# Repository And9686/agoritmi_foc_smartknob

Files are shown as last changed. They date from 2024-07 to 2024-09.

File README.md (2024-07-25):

# Algoritmi SmartKnob DevKit
## Motivation
This repository intends to achieve a development kit for a SmartKnob like the one from scottbez and allow it to be compatible with any microcontroller with dedicated firmware adaptable to any board. This DevKit design is inspired by NanoFoc DevKit by KatBinaris.

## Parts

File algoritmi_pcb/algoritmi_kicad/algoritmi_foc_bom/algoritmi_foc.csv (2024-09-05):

Reference | Value | Datasheet | Footprint | Qty | DNP | Manufacturer_Part_Number | Mouser Part Number | LCSC Electronics Part Number
C1 | 100nF 50V | http://www.samsungsem.com/kr/support/product-search/mlcc/CL10B104KB8NNWC.jsp | CAPC1608X90N | 1 |  | CL10B104KB8NNWC | 187-CL10B104KB8NNWC
C2 | 100nF 50V | http://www.samsungsem.com/kr/support/product-search/mlcc/CL10B104KB8NNWC.jsp | CAPC1608X90N | 1 |  | CL10B104KB8NNWC | 187-CL10B104KB8NNWC
C3 | 100nF 50V | http://www.samsungsem.com/kr/support/product-search/mlcc/CL10B104KB8NNWC.jsp | CAPC1608X90N | 1 |  | CL10B104KB8NNWC | 187-CL10B104KB8NNWC
C4 | 100nF 50V | http://www.samsungsem.com/kr/support/product-search/mlcc/CL10B104KB8NNWC.jsp | CAPC1608X90N | 1 |  | CL10B104KB8NNWC | 187-CL10B104KB8NNWC
C5 | 10uF 25V | https://datasheet.datasheetarchive.com/originals/distributors/Datasheets_SAMA/6a45835c9b7400e9b49c55c38a8ff4a2.pdf | CAPC2012X145N | 1 |  | CL21A106KAYNNNE | 187-CL21A106KAYNNNE
C7 | 4.7uF 25V | https://psearch.en.murata.com/capacitor/product/GCM21BC71E475KE36%23.html | CAPC2012X140N | 1 |  | GCM21BC71E475KE36K | 81-GCM21BC71E475KE6K
C8 | 4.7uF 25V | https://psearch.en.murata.com/capacitor/product/GCM21BC71E475KE36%23.html | CAPC2012X140N | 1 |  | GCM21BC71E475KE36K | 81-GCM21BC71E475KE6K
C9 | 10uF 25V | https://datasheet.datasheetarchive.com/originals/distributors/Datasheets_SAMA/6a45835c9b7400e9b49c55c38a8ff4a2.pdf | CAPC2012X145N | 1 |  | CL21A106KAYNNNE | 187-CL21A106KAYNNNE
C10 | 100nF 50V | http://www.samsungsem.com/kr/support/product-search/mlcc/CL10B104KB8NNWC.jsp | CAPC1608X90N | 1 |  | CL10B104KB8NNWC | 187-CL10B104KB8NNWC
D1 | STDBY | https://datasheet.datasheetarchive.com/originals/distributors/Datasheets_SAMA/f235664866caa647598714bb71411137.pdf | LEDM1620X150N | 1 |  | SML-D12M8WT86 | 755-SML-D12M8WT86
D2 | ERROR | https://datasheet.datasheetarchive.com/originals/distributors/Datasheets_SAMA/f235664866caa647598714bb71411137.pdf | LEDM1620X150N | 1 |  | SML-D12M8WT86 | 755-SML-D12M8WT86
IC2 | AP2114HA-3.3TRG1 | https://www.diodes.com//assets/Datasheets/AP2114.pdf | SOT230P700X180-4N | 1 |  | AP2114HA-3.3TRG1 | 621-AP2114HA-3.3TRG1
J1 | ~ |  | solder_pads:solder_pads_2mm_8 | 1 | DNP |  | 1
J2 | 53261-0371 |  | 532610371 | 1 |  | 53261-0371 | 538-53261-0371
J3 | SMM-115-02-S-D-LC-K-TR | https://suddendocs.samtec.com/prints/smm-1xx-xx-xx-d-xx-xx-x-xx-mkt.pdf | SMM11502SDLCKTR | 1 |  | SMM-115-02-S-D-LC-K-TR | 200-SMM11502SDLCKTR
MSW1 | ~ |  | solder_pads:solder_pads_4mm_3 | 1 |  |  | 906-XCF3Z1
MSW2 | ~ |  | solder_pads:solder_pads_4mm_3 | 1 |  |  | 906-XCF3Z1
MSW3 | ~ |  | solder_pads:solder_pads_4mm_3 | 1 |  |  | 906-XCF3Z1
MSW4 | ~ |  | solder_pads:solder_pads_4mm_3 | 1 |  |  | 906-XCF3Z1
R1 | 300R | https://industrial.panasonic.com/cdbs/www-data/pdf/RDP0000/AOA0000C337.pdf | ERJUP3 | 1 |  | ERJ-UP3F3000V | 667-ERJ-UP3F3000V
R2 | 300R | https://industrial.panasonic.com/cdbs/www-data/pdf/RDP0000/AOA0000C337.pdf | ERJUP3 | 1 |  | ERJ-UP3F3000V | 667-ERJ-UP3F3000V
R3 | 150m | https://www.koaspeer.com/pdfs/UR73V.pdf | RESC3216X70N | 1 |  | UR73VH2BTTDR150F | 660-UR73VH2BTTDR150F
R4 | 150m | https://www.koaspeer.com/pdfs/UR73V.pdf | RESC3216X70N | 1 |  | UR73VH2BTTDR150F | 660-UR73VH2BTTDR150F
R5 | 100K | https://www.mouser.co.uk/datasheet/2/54/Bourns_CMP_Datasheet_05.28.20-1854233.pdf | RESC1608X55N | 1 |  | CMP0603-FX-1003ELF | 652-CMP0603-FX-1003L
R6 | 100K | https://www.mouser.co.uk/datasheet/2/54/Bourns_CMP_Datasheet_05.28.20-1854233.pdf | RESC1608X55N | 1 |  | CMP0603-FX-1003ELF | 652-CMP0603-FX-1003L
R7 | 100K | https://www.mouser.co.uk/datasheet/2/54/Bourns_CMP_Datasheet_05.28.20-1854233.pdf | RESC1608X55N | 1 |  | CMP0603-FX-1003ELF | 652-CMP0603-FX-1003L
R8 | 100K | https://www.mouser.co.uk/datasheet/2/54/Bourns_CMP_Datasheet_05.28.20-1854233.pdf | RESC1608X55N | 1 |  | CMP0603-FX-1003ELF | 652-CMP0603-FX-1003L
R9 | 100K | https://www.mouser.co.uk/datasheet/2/54/Bourns_CMP_Datasheet_05.28.20-1854233.pdf | RESC1608X55N | 1 |  | CMP0603-FX-1003ELF | 652-CMP0603-FX-1003L
R10 | 100K | https://www.mouser.co.uk/datasheet/2/54/Bourns_CMP_Datasheet_05.28.20-1854233.pdf | RESC1608X55N | 1 |  | CMP0603-FX-1003ELF | 652-CMP0603-FX-1003L
R11 | 300R | https://industrial.panasonic.com/cdbs/www-data/pdf/RDP0000/AOA0000C337.pdf | ERJUP3 | 1 |  | ERJ-UP3F3000V | 667-ERJ-UP3F3000V
R12 | 300R | https://industrial.panasonic.com/cdbs/www-data/pdf/RDP0000/AOA0000C337.pdf | ERJUP3 | 1 |  | ERJ-UP3F3000V | 667-ERJ-UP3F3000V
R13 | 300R | https://industrial.panasonic.com/cdbs/www-data/pdf/RDP0000/AOA0000C337.pdf | ERJUP3 | 1 |  | ERJ-UP3F3000V | 667-ERJ-UP3F3000V
R14 | 300R | https://industrial.panasonic.com/cdbs/www-data/pdf/RDP0000/AOA0000C337.pdf | ERJUP3 | 1 |  | ERJ-UP3F3000V | 667-ERJ-UP3F3000V
U1 | TMC6300-LA-T | TMC6300-LA-T | SamacSys_Parts:QFN40P300X300X90-21N | 1 |  | TMC6300-LA-T | 700-TMC6300-LA-T
U2 | MT6701CT-STD | https://www.lcsc.com/datasheet/lcsc_datasheet_2109011830_Magn-Tek-MT6701CT-STD_C2856764.pdf | Package_SO:SOIC-8_3.9x4.9mm_P1.27mm | 1 |  | MT6701CT-STD |  | C2856764

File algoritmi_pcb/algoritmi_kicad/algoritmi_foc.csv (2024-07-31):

Source: | C:\Users\aluno\Documents\GitHub\agoritmi_foc_smartknob\algoritmi_pcb\algoritmi_kicad\algoritmi_foc.kicad_sch
Date: | 7/31/2024 11:25:34 AM
Tool: | Eeschema 7.0.10
Generator: | C:\Program Files\KiCad\7.0\bin\scripting\plugins/bom_csv_grouped_by_value.py
Component Count: | 35
Collated Components:
Item | Qty | Reference(s) | Value | LibPart | Footprint | Datasheet | DNP | Height | Link | Manufacturer_Name | Manufacturer_Part_Number | Mouser | Mouser Part Number | Mouser Price/Stock
1 | 4 | C1, C2, C3, C4 | 100nF 50V | :CL10B104KB8NNWC_1 | CAPC1608X90N | http://www.samsungsem.com/kr/support/product-search/mlcc/CL10B104KB8NNWC.jsp |  | 0.9 |  | SAMSUNG | CL10B104KB8NNWC |  | 187-CL10B104KB8NNWC | https://www.mouser.co.uk/ProductDetail/Samsung-Electro-Mechanics/CL10B104KB8NNWC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
2 | 1 | C5 | 10uF 25V | :CL21A106KAYNNNE_1 | CAPC2012X145N | https://datasheet.datasheetarchive.com/originals/distributors/Datasheets_SAMA/6a45835c9b7400e9b49c55c38a8ff4a2.pdf |  | 1.45 |  | SAMSUNG | CL21A106KAYNNNE |  | 187-CL21A106KAYNNNE | https://www.mouser.co.uk/ProductDetail/Samsung-Electro-Mechanics/CL21A106KAYNNNE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
3 | 1 | C6 | 1uF | SamacSys_Parts:CL10A105KA8NNNC | CAPC1608X90N |  |  | 0.9 |  | SAMSUNG | CL10A105KA8NNNC |  | 187-CL10A105KA8NNNC | https://www.mouser.co.uk/ProductDetail/Samsung-Electro-Mechanics/CL10A105KA8NNNC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
4 | 2 | C7, C8 | 4.7uF 25V | :GCM21BC71E475KE36K_1 | CAPC2012X140N | https://psearch.en.murata.com/capacitor/product/GCM21BC71E475KE36%23.html |  | 1.4 |  | Murata Electronics | GCM21BC71E475KE36K |  | 81-GCM21BC71E475KE6K | https://www.mouser.co.uk/ProductDetail/Murata-Electronics/GCM21BC71E475KE36K?qs=dNBNMwHp2UBfaO4Bu7xrag%3D%3D
5 | 1 | C9 | 10uF 25V | SamacSys_Parts:CL21A106KAYNNNE | CAPC2012X145N | https://datasheet.datasheetarchive.com/originals/distributors/Datasheets_SAMA/6a45835c9b7400e9b49c55c38a8ff4a2.pdf |  | 1.45 |  | SAMSUNG | CL21A106KAYNNNE |  | 187-CL21A106KAYNNNE | https://www.mouser.co.uk/ProductDetail/Samsung-Electro-Mechanics/CL21A106KAYNNNE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
6 | 1 | D1 | STDBY | :SML-D12M8WT86_2 | LEDM1620X150N | https://datasheet.datasheetarchive.com/originals/distributors/Datasheets_SAMA/f235664866caa647598714bb71411137.pdf |  | 1.5 |  | ROHM Semiconductor | SML-D12M8WT86 |  | 755-SML-D12M8WT86 | https://www.mouser.co.uk/ProductDetail/ROHM-Semiconductor/SML-D12M8WT86?qs=4kLU8WoGk0vGWtDreJ93zQ%3D%3D
7 | 1 | D2 | ERROR | :SML-D12M8WT86_1 | LEDM1620X150N | https://datasheet.datasheetarchive.com/originals/distributors/Datasheets_SAMA/f235664866caa647598714bb71411137.pdf |  | 1.5 |  | ROHM Semiconductor | SML-D12M8WT86 |  | 755-SML-D12M8WT86 | https://www.mouser.co.uk/ProductDetail/ROHM-Semiconductor/SML-D12M8WT86?qs=4kLU8WoGk0vGWtDreJ93zQ%3D%3D
8 | 1 | IC1 | MA710GQ-Z | SamacSys_Parts:MA710GQ-Z | QFN50P300X300X100-17N-D |  |  | 1 |  | Monolithic Power Systems (MPS) | MA710GQ-Z |  | 946-MA710GQ-Z | https://www.mouser.co.uk/ProductDetail/Monolithic-Power-Systems-MPS/MA710GQ-Z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
9 | 1 | IC2 | AP2114HA-3.3TRG1 | SamacSys_Parts:AP2114HA-3.3TRG1 | SOT230P700X180-4N | https://www.diodes.com//assets/Datasheets/AP2114.pdf |  | 1.8 |  | Diodes Incorporated | AP2114HA-3.3TRG1 |  | 621-AP2114HA-3.3TRG1 | https://www.mouser.co.uk/ProductDetail/Diodes-Incorporated/AP2114HA-3.3TRG1?qs=M%2FOdCRO8QQ3KWhA9Gt6VoQ%3D%3D
10 | 1 | J1 | ~ | solder_pad:solder_pad_2mm_8 | solder_pads:solder_pads_2mm_8
11 | 1 | J2 | 53261-0371 | SamacSys_Parts:53261-0371 | 532610371 |  |  | 3.6 |  | Molex | 53261-0371 |  | 538-53261-0371 | https://www.mouser.co.uk/ProductDetail/Molex/53261-0371?qs=%252B72YyncTwW%252BTQBxAO1kJjA%3D%3D
12 | 1 | J3 | SMM-115-02-S-D-LC-K-TR | SamacSys_Parts:SMM-115-02-S-D-LC-K-TR | SMM11502SDLCKTR | https://suddendocs.samtec.com/prints/smm-1xx-xx-xx-d-xx-xx-x-xx-mkt.pdf |  | 3.81 |  | SAMTEC | SMM-115-02-S-D-LC-K-TR |  | 200-SMM11502SDLCKTR | https://www.mouser.co.uk/ProductDetail/Samtec/SMM-115-02-S-D-LC-K-TR?qs=Cqqh%252BS766wmCL5XLNTE7Jg%3D%3D
13 | 4 | MSW1, MSW2, MSW3, MSW4 | ~ | solder_pad:solder_pad_4mm_3 | solder_pads:solder_pads_4mm_3 |  |  |  | https://pt.mouser.com/ProductDetail/Saia-Burgess/XCF3Z1?qs=lDMevKbHVysAJU%252Bj62uRPA%3D%3D |  |  | 906-XCF3Z1
14 | 2 | R1, R2 | 300R | :ERJ-UP3F3000V_1 | ERJUP3 | https://industrial.panasonic.com/cdbs/www-data/pdf/RDP0000/AOA0000C337.pdf |  | 0.55 |  | Panasonic | ERJ-UP3F3000V |  | 667-ERJ-UP3F3000V | https://www.mouser.co.uk/ProductDetail/Panasonic/ERJ-UP3F3000V?qs=GedFDFLaBXGMAT9BybhSQA%3D%3D
15 | 2 | R3, R4 | 150m | :UR73VH2BTTDR150F_1 | RESC3216X70N | https://www.koaspeer.com/pdfs/UR73V.pdf |  | 0.7 |  | KOA Speer | UR73VH2BTTDR150F
16 | 6 | R5, R6, R7, R8, R9, R10 | 100K | :CMP0603-FX-1003ELF_1 | RESC1608X55N | https://www.mouser.co.uk/datasheet/2/54/Bourns_CMP_Datasheet_05.28.20-1854233.pdf |  | 0.55 |  | Bourns | CMP0603-FX-1003ELF |  | 652-CMP0603-FX-1003L | https://www.mouser.co.uk/ProductDetail/Bourns/CMP0603-FX-1003ELF?qs=TiOZkKH1s2SZ50zoNdROqA%3D%3D
17 | 4 | R11, R12, R13, R14 | 300R | SamacSys_Parts:ERJ-UP3F3000V | ERJUP3 | https://industrial.panasonic.com/cdbs/www-data/pdf/RDP0000/AOA0000C337.pdf |  | 0.55 |  | Panasonic | ERJ-UP3F3000V |  | 667-ERJ-UP3F3000V | https://www.mouser.co.uk/ProductDetail/Panasonic/ERJ-UP3F3000V?qs=GedFDFLaBXGMAT9BybhSQA%3D%3D
18 | 1 | U1 | TMC6300-LA-T | TMC6300:TMC6300-LA-T | SamacSys_Parts:QFN40P300X300X90-21N | TMC6300-LA-T

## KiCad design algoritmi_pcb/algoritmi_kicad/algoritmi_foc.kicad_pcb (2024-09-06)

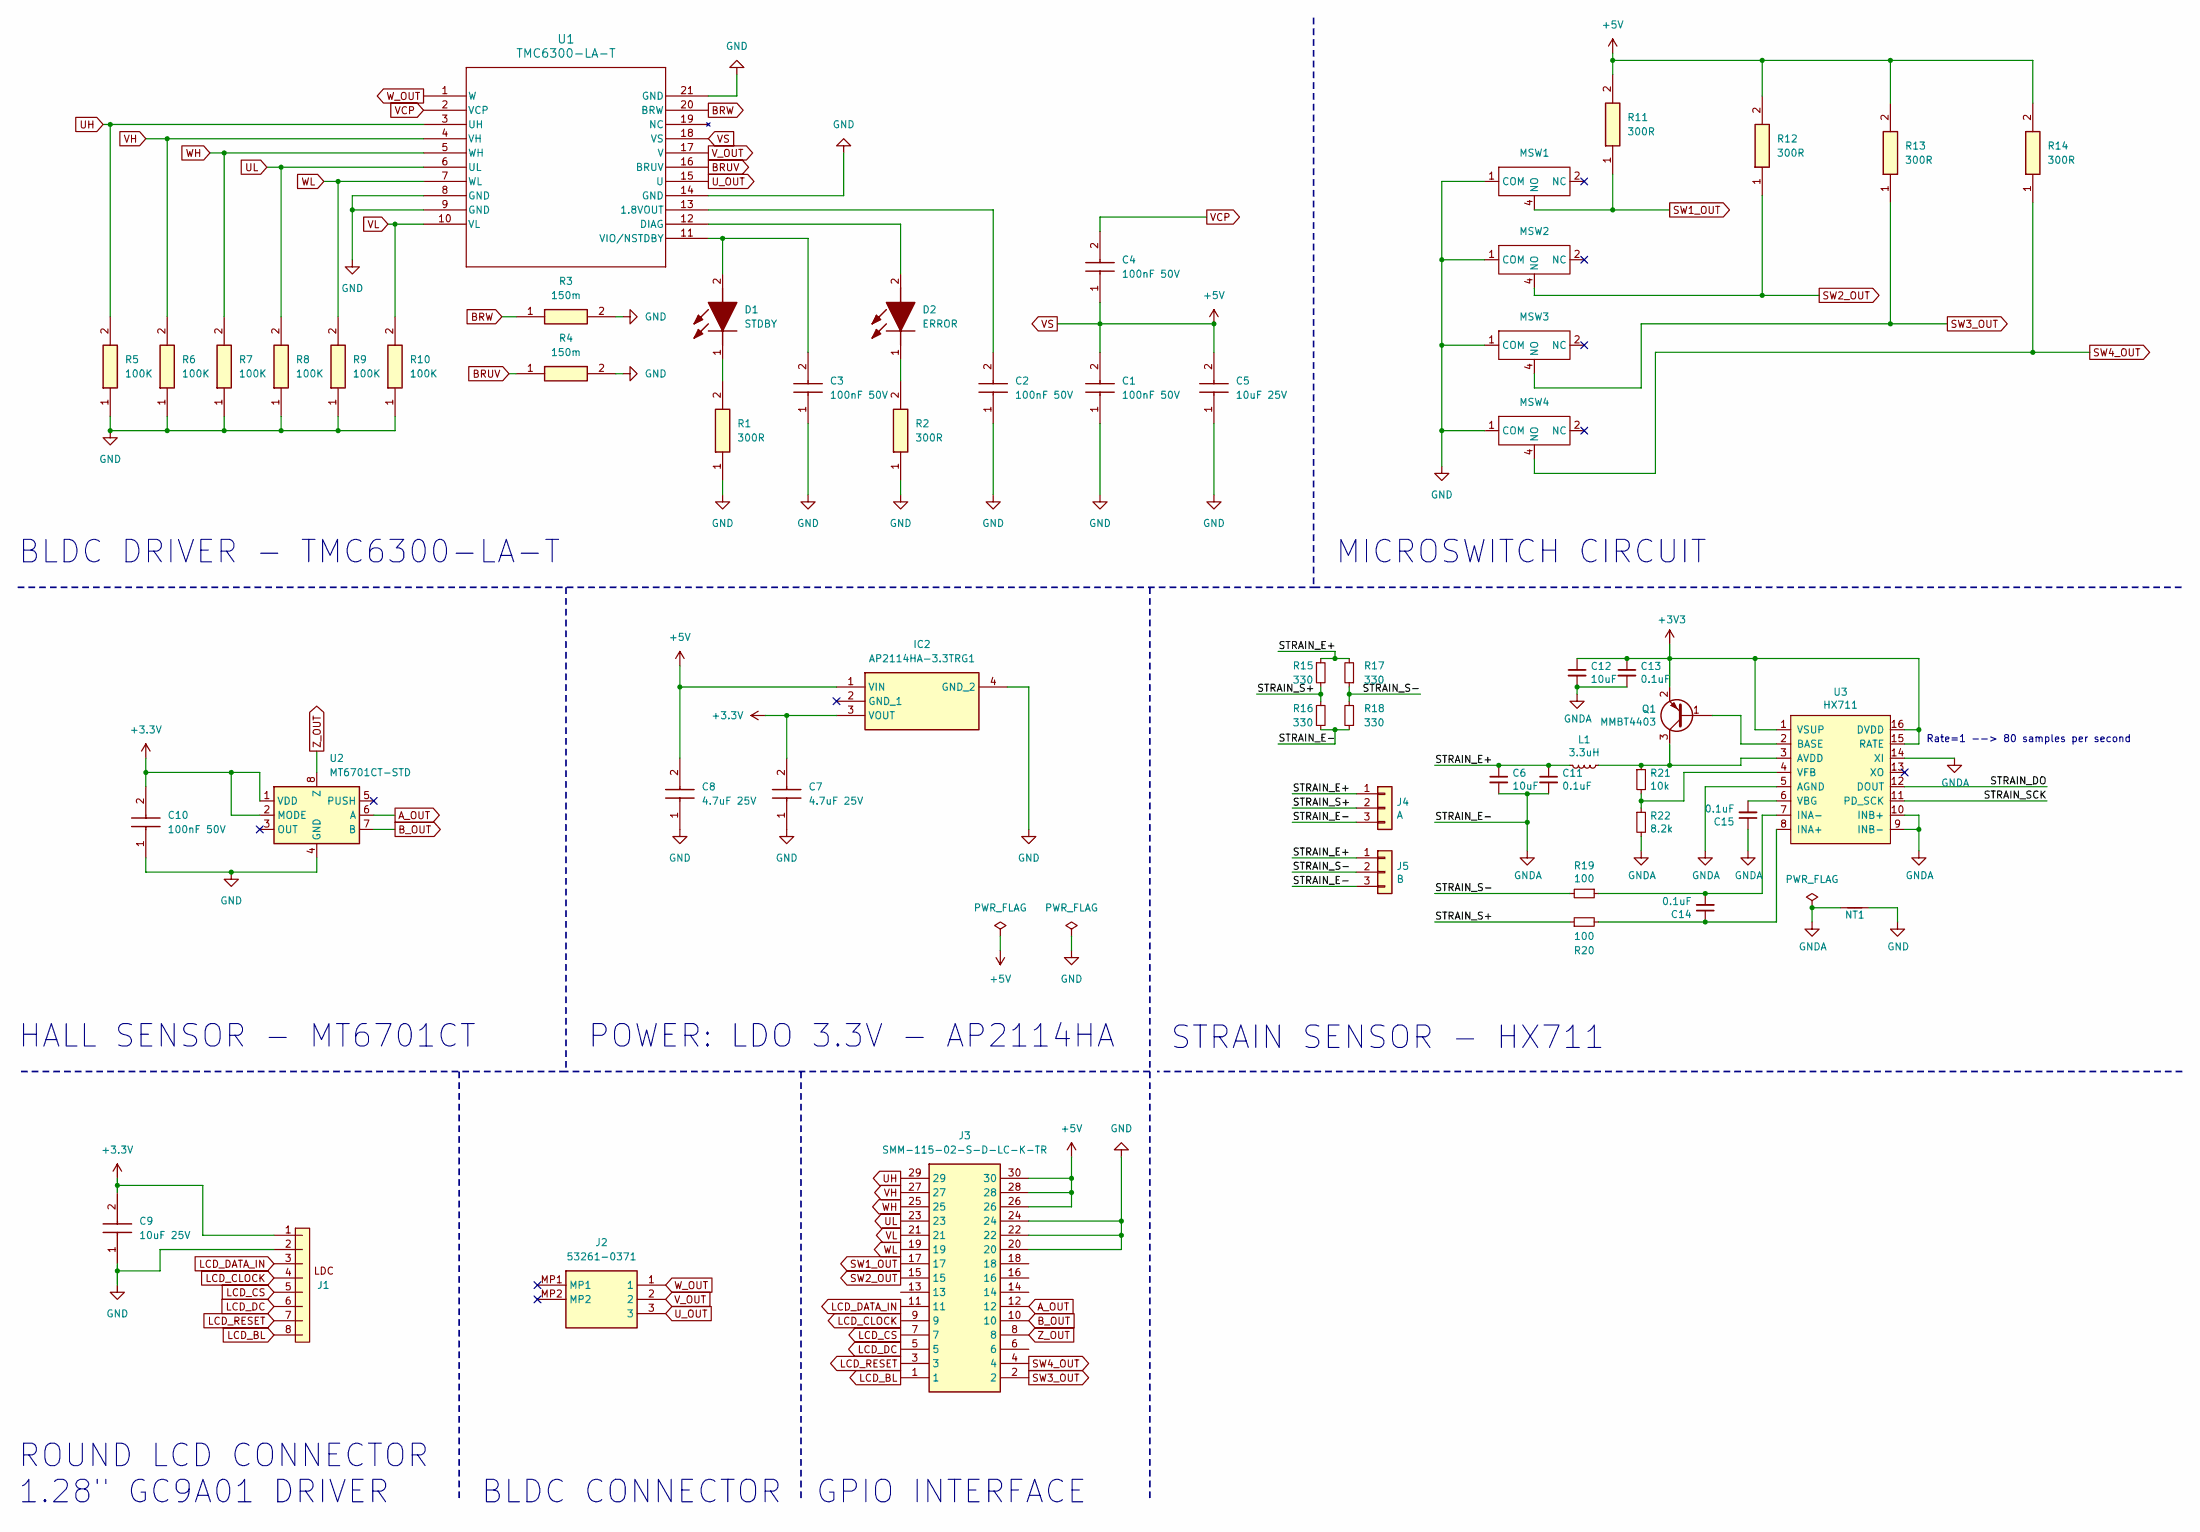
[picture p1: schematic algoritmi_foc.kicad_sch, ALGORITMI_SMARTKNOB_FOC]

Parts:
C1, C2, C3, C4, C10: 100nF 50V; CAPC1608X90N; Mouser Part Number 187-CL10B104KB8NNWC
C5, C9: 10uF 25V; CAPC2012X145N; Mouser Part Number 187-CL21A106KAYNNNE
C6, C12: 10uF; C_0805_2012Metric; LCSC C2922480
C7, C8: 4.7uF 25V; CAPC2012X140N; Mouser Part Number 81-GCM21BC71E475KE6K
C11, C13, C14, C15: 0.1uF; C_0603_1608Metric; LCSC C1591
D1: STDBY; LEDM1620X150N; Mouser Part Number 755-SML-D12M8WT86
D2: ERROR; LEDM1620X150N; Mouser Part Number 755-SML-D12M8WT86
IC2: AP2114HA-3.3TRG1; SOT230P700X180-4N; Mouser Part Number 621-AP2114HA-3.3TRG1
J1: solder_pads_2mm_8; Mouser Part Number 1
J2: 53261-0371; 532610371; Mouser Part Number 538-53261-0371
J3: SMM-115-02-S-D-LC-K-TR; SMM11502SDLCKTR; Mouser Part Number 200-SMM11502SDLCKTR
J4: A; SolderPads_2mm_3_STRAIN
J5: B; SolderPads_2mm_3_STRAIN
L1: 3.3uH; L_0805_2012Metric; LCSC C307744
MSW1, MSW2, MSW3, MSW4: solder_pads_4mm_3; Mouser Part Number 906-XCF3Z1; Mouser 906-XCF3Z1
NT1: NetTie_2; NetTie-2_SMD_Pad0.5mm
Q1: MMBT4403; SOT-23; LCSC C78864
R1, R2, R11, R12, R13, R14: 300R; ERJUP3; Mouser Part Number 667-ERJ-UP3F3000V
R3, R4: 150m; RESC3216X70N; Mouser Part Number 660-UR73VH2BTTDR150F
R5, R6, R7, R8, R9, R10: 100K; RESC1608X55N; Mouser Part Number 652-CMP0603-FX-1003L
R15, R16, R17, R18: 330; R_2512_6332Metric; LCSC C19866
R19, R20: 100; R_0603_1608Metric; LCSC C319953
R21: 10k; R_0603_1608Metric; LCSC C98220
R22: 8.2k; R_0603_1608Metric; LCSC C114637
U1: TMC6300-LA-T; QFN40P300X300X90-21N; Manufacturer_Part_Number TMC6300-LA-T; Mouser Part Number 700-TMC6300-LA-T
U2: MT6701CT-STD; SOIC-8_3.9x4.9mm_P1.27mm; Manufacturer_Part_Number MT6701CT-STD; LCSC Electronics Part N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 C2856764
U3: HX711; SOIC-16_3.9x9.9mm_P1.27mm; LCSC C43656

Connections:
+3V3: C12.1, C13.1, Q1.2 (E), U3.1 (VSUP), U3.15 (RATE), U3.16 (DVDD)
/STRAIN_DO: U3.12 (DOUT)
/STRAIN_S+: J4.2, R15.2, R16.1, R20.1
/STRAIN_S-: J5.2, R17.1, R18.2, R19.2
/STRAIN_SCK: U3.11 (PD_SCK)
A_OUT: J3.12, U2.6 (A)
BRUV: R4.1, U1.16 (BRUV)
BRW: R3.1, U1.20 (BRW)
B_OUT: J3.10, U2.7 (B)
LCD_BL: J1.8, J3.1
LCD_CLOCK: J1.4, J3.9
LCD_CS: J1.5, J3.7
LCD_DATA_IN: J1.3, J3.11
LCD_DC: J1.6, J3.5
LCD_RESET: J1.7, J3.3
unnamed: C3.2, D1.2 (A), U1.11 (VIO/NSTDBY)
unnamed: D1.1 (K), R1.2
unnamed: D2.2 (A), U1.12 (DIAG)
unnamed: D2.1 (K), R2.2
unnamed: Q1.1 (B), U3.2 (BASE)
unnamed: L1.1, Q1.3 (C), R21.1, U3.3 (AVDD)
unnamed: C2.2, U1.13 (1.8VOUT)
unnamed: C14.1, R20.2, U3.8 (INA+)
unnamed: C14.2, R19.1, U3.7 (INA-)
unnamed: C15.2, U3.6 (VBG)
unnamed: R21.2, R22.1, U3.4 (VFB)
SW1_OUT: J3.17, MSW1.4 (NO), R11.1
SW2_OUT: J3.15, MSW2.4 (NO), R12.1
SW3_OUT: J3.2, MSW3.4 (NO), R13.1
SW4_OUT: J3.4, MSW4.4 (NO), R14.1
UH: J3.29, R5.2, U1.3 (UH)
UL: J3.23, R8.2, U1.6 (UL)
U_OUT: J2.3, U1.15 (U)
VCP: C4.2, U1.2 (VCP)
VH: J3.27, R6.2, U1.4 (VH)
VL: J3.21, R10.2, U1.10 (VL)
VS: C1.2, C4.1, C5.2, C8.2, IC2.1 (VIN), J3.26, J3.28, J3.30, R11.2, R12.2, R13.2, R14.2, U1.18 (VS)
V_OUT: J2.2, U1.17 (V)
WH: J3.25, R7.2, U1.5 (WH)
WL: J3.19, R9.2, U1.7 (WL)
W_OUT: J2.1, U1.1 (W)
Z_OUT: J3.8, U2.8 (Z)

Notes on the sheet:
STRAIN SENSOR - HX711
MICROSWITCH CIRCUIT
GPIO INTERFACE
BLDC DRIVER - TMC6300-LA-T
HALL SENSOR - MT6701CT
BLDC CONNECTOR
ROUND LCD CONNECTOR 1.28" GC9A01 DRIVER
Rate=1 --> 80 samples per second
POWER: LDO 3.3V - AP2114HA

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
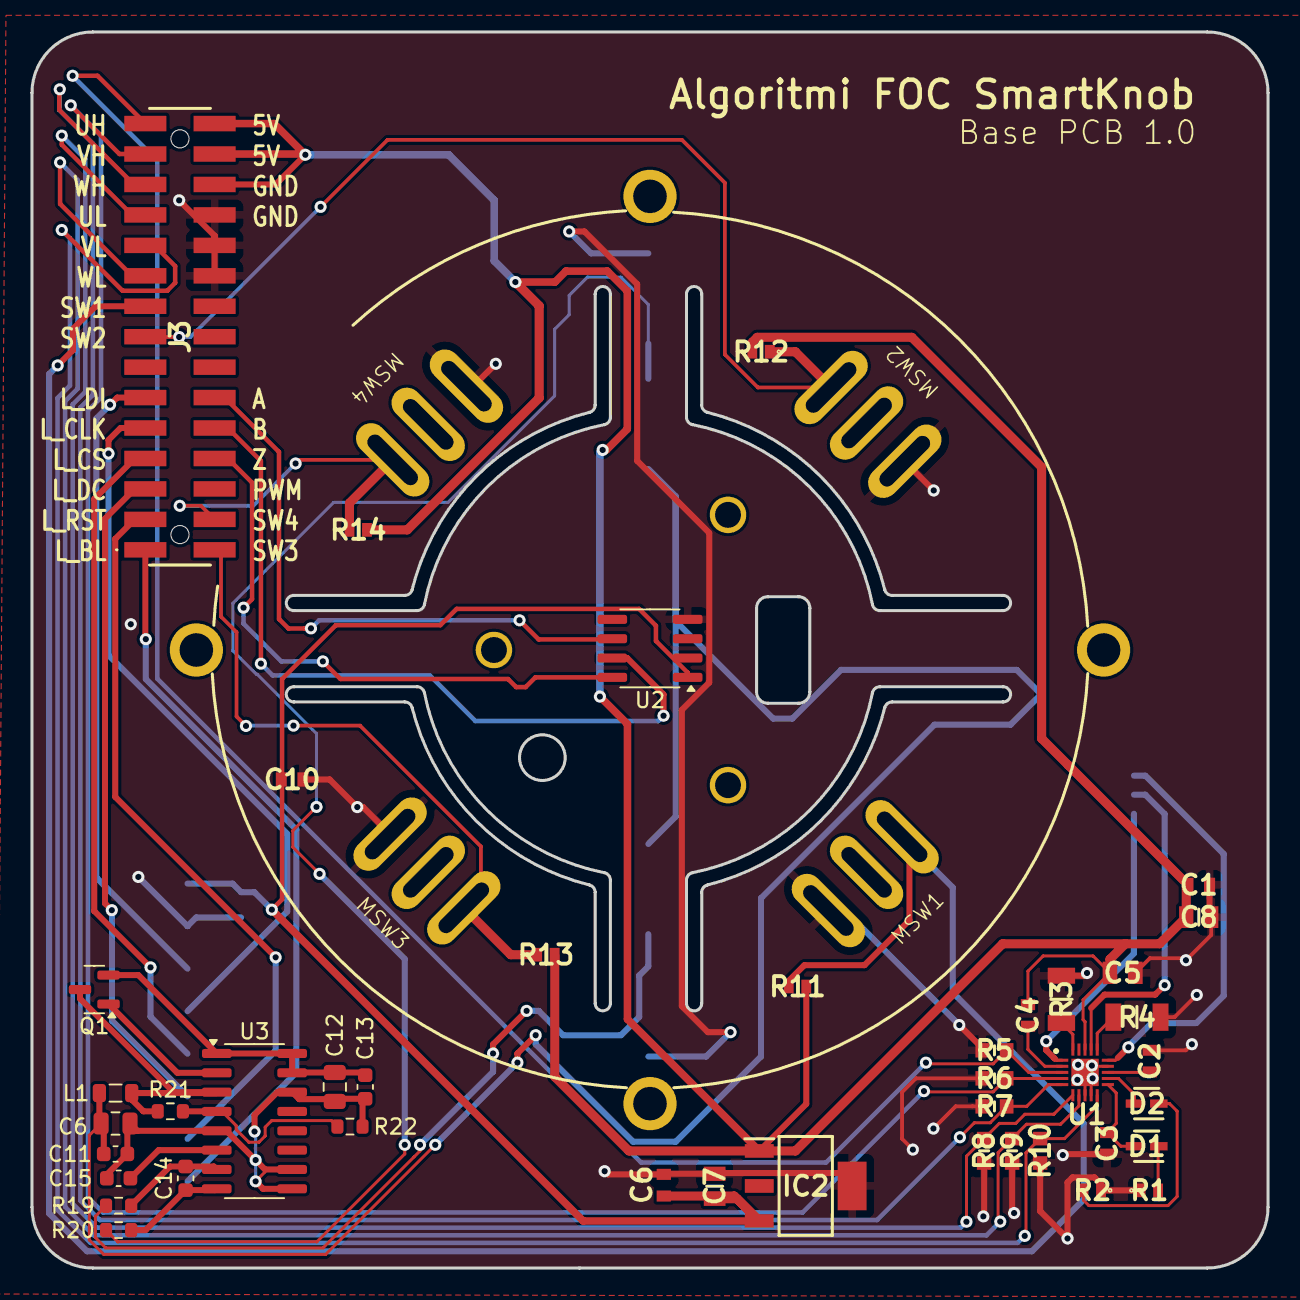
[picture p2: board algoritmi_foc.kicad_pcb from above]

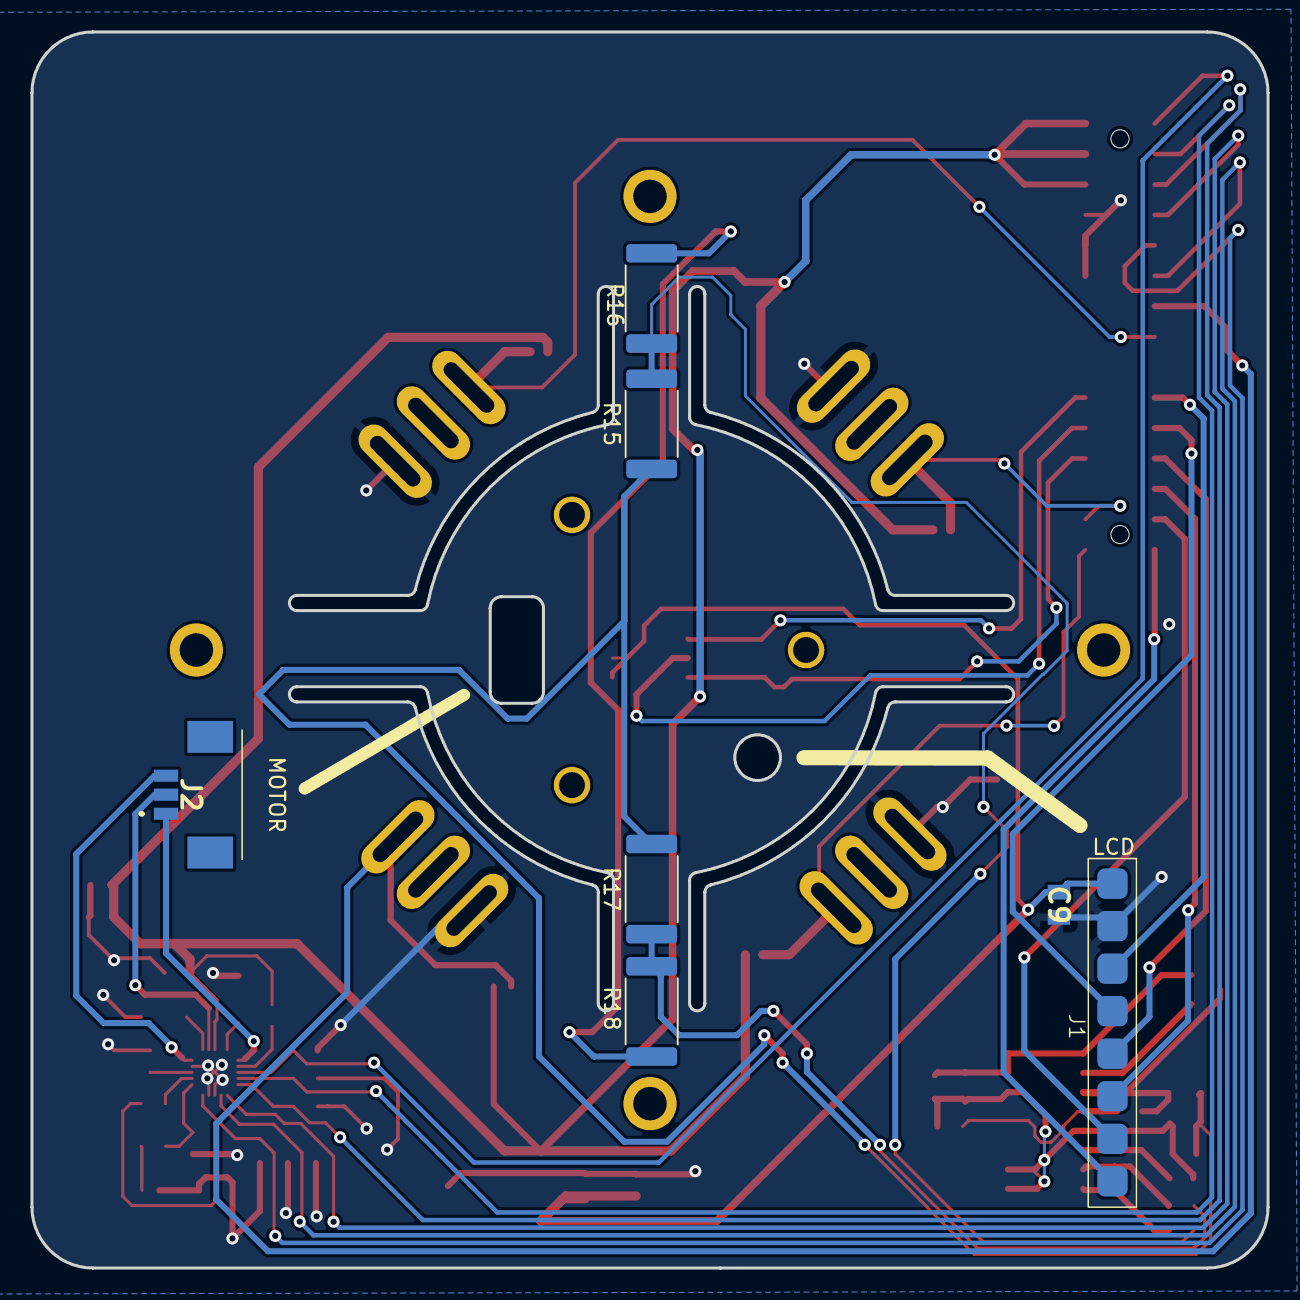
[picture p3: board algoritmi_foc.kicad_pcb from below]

Board: 2 copper layers, 81.2 x 81.2 mm, 60 parts (7 on the bottom side), 44 nets.

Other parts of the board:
C6#2: 10uF; C_0805_2012Metric
H1, H2, H3: MotorHole; MountingHole_M1.6
H4, H5, H6, H7: MountHole; MountingHole_2.2mm_M2_ISO7380_Pad_NonVirtual

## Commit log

2024-07-22 Work Till Now
    PCB schematics unfinished
    [algoritmi_foc.kicad_pcb, algoritmi_foc.kicad_sch]
2024-07-23 Updates to the schematics
    [algoritmi_foc.kicad_sch]
2024-07-24 Schematics: Added Power and Encoder
    [algoritmi_foc.kicad_sch]
2024-07-24 Component Footprints Added
2024-07-25 Final Schematics and started PCB design
    [algoritmi_foc.kicad_pcb, algoritmi_foc.kicad_sch]
2024-07-26 Update PCB and Design
    Design: added the connector for the motor.
    PCB: added some constraints and essentially connected all the components to the TMC6300-LA-T.
    [algoritmi_foc.kicad_pcb, algoritmi_foc.kicad_sch]
2024-07-26 Components Update
    Added the component for the Motor connector.
2024-07-29 More PCB and Schematics Design
    Also added components to the library.
    [algoritmi_foc.kicad_pcb, algoritmi_foc.kicad_sch]
2024-07-30 PCB v0 Finished
    PCB design ended, version 0
    [algoritmi_foc.kicad_pcb]
2024-07-31 added gerber and drill files
    [algoritmi_foc-B_Cu.gbr, algoritmi_foc-B_Mask.gbr, algoritmi_foc-B_Paste.gbr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]
2024-09-02 my laptop version updated
    [algoritmi_foc.kicad_sch]
2024-09-02 finished version_1
    doesn't have the presure sensitive part
    [algoritmi_foc-B_Cu.gbr, algoritmi_foc-B_Mask.gbr, algoritmi_foc-B_Paste.gbr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]
2024-09-02 extra updates version 1
    [algoritmi_foc.kicad_pcb]
2024-09-05 New updates
    [algoritmi_foc.csv, algoritmi_foc.kicad_pcb, algoritmi_foc.kicad_sch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]
2024-09-05 adding the presure sensitive click pcb
    I forgot to put it in the right position :)
    [algoritmi_foc.kicad_pcb, algoritmi_foc.kicad_sch]
2024-09-06 updated positioning of presure sensors
    NOTE: the GND on the presure sensor circuit is not connected to the GND of the whole circuit.
    [algoritmi_foc.kicad_pcb]
2024-09-06 updates
    Just opened the file and closed, the kicad always generates autosaves.
